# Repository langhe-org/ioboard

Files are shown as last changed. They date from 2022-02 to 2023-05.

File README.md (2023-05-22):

# ioboard

This circuit board is the interface between a Beaglebone Black and the rest of the greenhouse components.

## Ordering

The part numbers in the BOM and CPL included in the release are generated for JLC PCB. Alternative part numbers will have to be used for other fabrication houses.

## Assembly BOM

The following components are not included in the PCBA and must be purchased and soldered on separately:

- 1x CUI PDQE20-Q24-S5-D
- 2x Mornsun BO505S-1RW3
- 8x Phoenix Contact 1945119
- 4x Phoenix Contact 1945122

## Mating Connectors

Part numbers to mate the the headers:

- 8x Phoenix Contact 1984031
- 4x Phoenix Contact 1984345

## Enclosure

This board is designed to be housed in a Polycase WH-16 enclosure.

https://www.polycase.com/wh-16

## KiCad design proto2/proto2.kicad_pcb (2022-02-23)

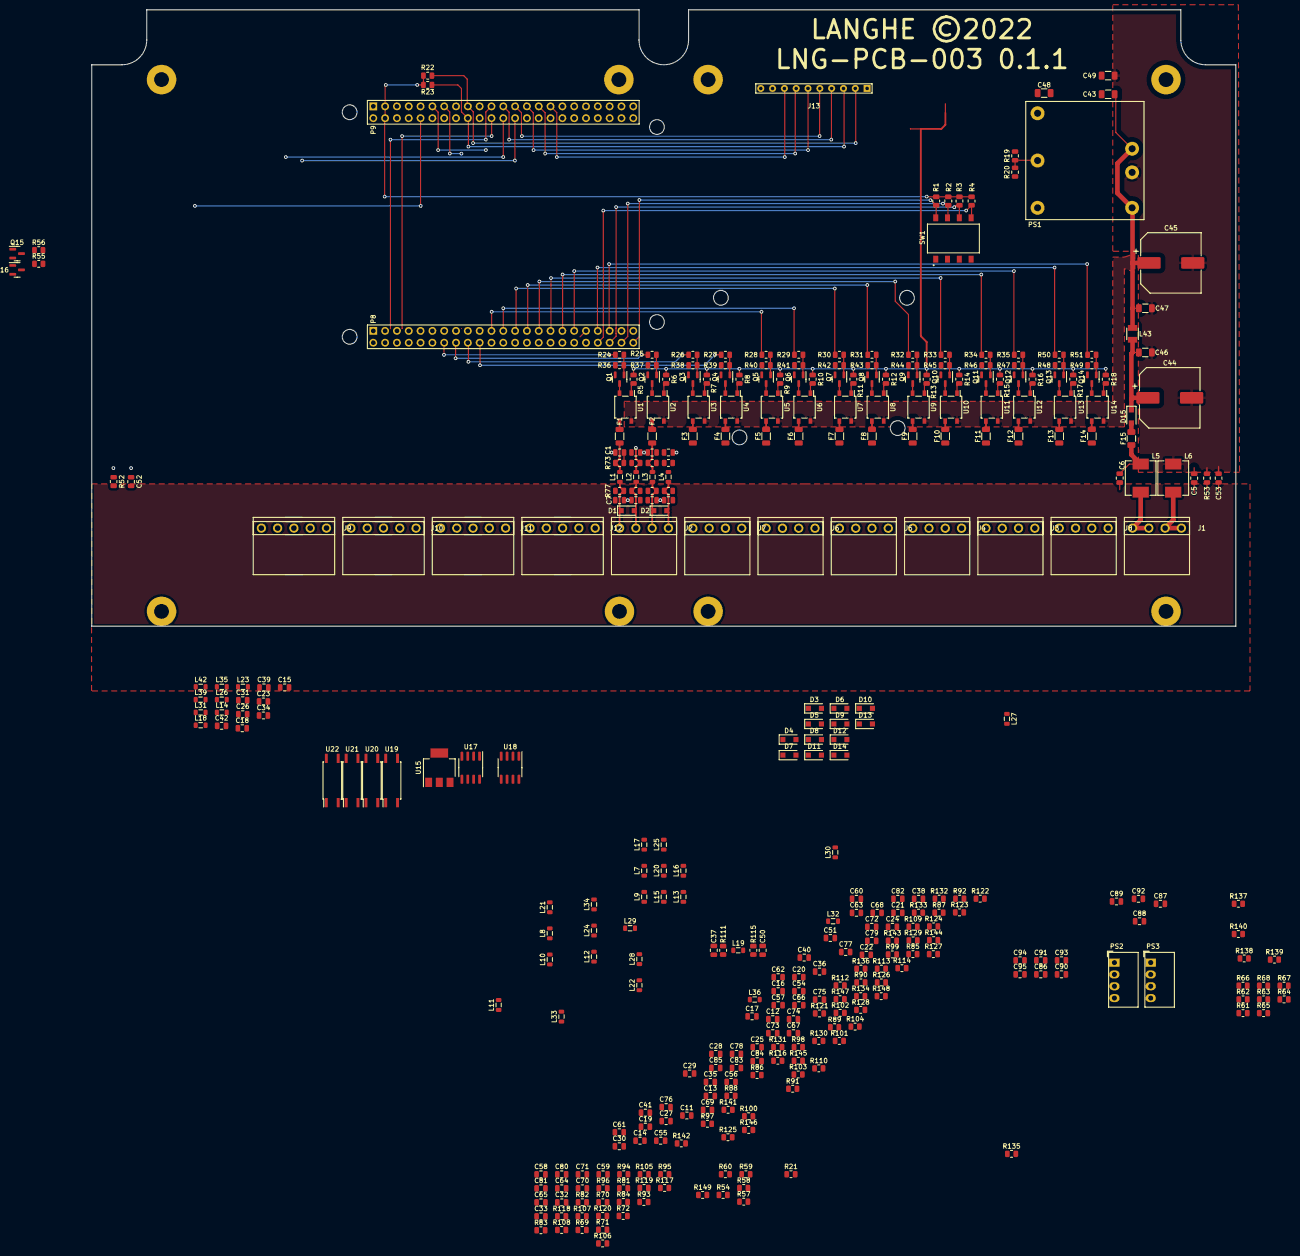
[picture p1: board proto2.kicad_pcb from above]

Board: 4 copper layers, 245.9 x 132.5 mm, 369 parts (0 on the bottom side), 250 nets.

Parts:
BB1: BeagleBone; BeagleBone_UpsideDown
C1, C2, C3, C4, C5, C6, C7, C8, C9, C10, C11, C12, C13, C14, C15, C16, C17, C18, C19, C20, C21, C22, C23, C24, C25, C26, C27, C28, C29, C30, C31, C32, C33, C34, C35, C36, C37, C38, C39, C40, C41, C42, C50, C51, C54, C55, C56, C57, C58, C59, C60, C61, C62, C63, C64, C65, C66, C67, C68, C69, C70, C71, C72, C73, C74, C75, C76, C77, C78, C79, C80, C81, C82, C83, C84, C85, C86, C87, C88, C89, C90, C91, C92, C93, C94, C95: 10uF; C_0805_2012Metric
C43, C49: 1nF 2kV; C_1206_3216Metric
C44, C45: 330uF; CP_Elec_13x12.5
C46, C47: 4.7uF; C_1206_3216Metric
C48: 100uF; C_1206_3216Metric
C52, C53: 0.1uF; C_0805_2012Metric
D1, D2, D3, D4, D5, D6, D7, D8, D9, D10, D11, D12, D13, D14, D15: D_Small_ALT; D_SOD-123F
F1, F2, F3, F4, F5, F6, F7, F8, F9, F10, F11, F12, F13, F14: 0.5A; R_1206_3216Metric
F15: 1A; R_1206_3216Metric
J1: Main Power; Phoenix_Contact_PST_4
J2, J3, J4, J5, J6, J7, J8: Output; Phoenix_Contact_PST_4
J9, J10, J11, J12: Device; Phoenix_Contact_PST_5
J13: Daughter Card; Proto2_DaughterCard
L1, L2, L3, L4, L7, L8, L9, L10, L11, L12, L13, L14, L15, L16, L17, L18, L19, L20, L21, L22, L23, L24, L25, L26, L27, L28, L29, L30, L31, L32, L33, L34, L35, L36, L39, L42: 10uH 500mA; L_0805_2012Metric
L5, L6: 2.2uH 7A; Coilmax_MS0630-2R2M
L43: 2.2uH 1.6A; Murata_LQH32PN2R2NN0L
Outline: Polycase_DC96
PS1: CUI PDQE20-Q24-S5-D; CUI_PDQE20
PS2, PS3: B0505S-1WR3; Converter_DCDC_Murata_MEE1SxxxxSC_THT
Q1, Q2, Q3, Q4, Q5, Q6, Q7, Q8, Q9, Q10, Q11, Q12, Q13, Q14, Q15: 2N7002; SOT-23
Q16: AO3401A; SOT-23
R1, R2, R3, R4, R21, R57, R65, R66, R67, R68: 10K; R_0805_2012Metric
R5, R6, R7, R8, R9, R10, R11, R12, R13, R14, R15, R16, R17, R18: 433R; R_0805_2012Metric
R19, R20: R Trim; C_0805_2012Metric
R22, R23, R137, R138: 4.7K; R_0805_2012Metric
R24, R25, R26, R27, R28, R29, R30, R31, R32, R33, R34, R35, R50, R51, R55, R61, R62, R63, R64: 1K; R_0805_2012Metric
R36, R37, R38, R39, R40, R41, R42, R43, R44, R45, R46, R47, R48, R49, R56: 27K; R_0805_2012Metric
R52, R53, R54, R58, R59, R60, R69, R70, R71, R72, R73, R74, R75, R76, R77, R78, R79, R80, R81, R82, R83, R84, R85, R86, R87, R88, R89, R90, R91, R92, R93, R94, R95, R96, R97, R98, R99, R100, R101, R102, R103, R104, R105, R106, R107, R108, R109, R110, R111, R112, R113, R114, R115, R116, R117, R118, R119, R120, R121, R122, R123, R124, R125, R126, R127, R128, R129, R130, R131, R132, R133, R134, R135, R136, R141, R142, R143, R144, R145, R146, R147, R148, R149: 0R; R_0805_2012Metric
R139, R140: 120R; R_0805_2012Metric
SW1: SW_DIP_x04; CUI_DS04-254-2-04BK-SMT
U1, U2, U3, U4, U5, U6, U7, U8, U9, U10, U11, U12, U13, U14: AQY282SX; SO-4_4.4x4.3mm_P2.54mm
U15: AMS1117-3.3; SOT-223-3_TabPin2
U17: ISO1540; SOIC-8_3.9x4.9mm_P1.27mm
U18: NSI8021N; SOIC-8_3.9x4.9mm_P1.27mm
U19, U20, U21, U22: EL817; SO-4_7.6x3.6mm_P2.54mm

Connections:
3V3_I2C: C91.1, R137.1, R138.1, U15.2 (VO)
5V_I2C: C88.1, C89.1, C90.1, L31.1, PS2.4 (+Vout), R105.1, U15.3 (VI), U17.8 (VCC2)
5V_UART: C94.1, C95.1, L39.1, PS3.4 (+Vout), R117.1, U18.8 (VDD2)
+3V3: BB1.9.3 (VDD_3V3), BB1.9.4 (VDD_3V3), C93.1, R1.1, R2.1, R3.1, R4.1, R21.1, R22.1, R23.1, R65.1, R66.1, R67.1, R68.1, U18.1 (VDD1)
+5V: BB1.9.5 (VDD_5V), BB1.9.6 (VDD_5V), Q16.2 (S), R5.2, R6.2, R7.2, R8.2, R9.2, R10.2, R11.2, R12.2, R13.2, R14.2, R15.2, R16.2, R17.2, R18.2, R57.1, R149.1
+5VP: C86.1, C87.1, C92.1, PS2.2 (+Vin), PS3.2 (+Vin), Q16.3 (D), R149.2, U17.1 (VCC1)
+24V: C43.2, C45.1, C47.1, L43.2, PS1.1 (CTRL), PS1.3 (Vin), U1.4, U2.4, U3.4, U4.4, U5.4, U6.4, U7.4, U8.4, U9.4, U10.4, U11.4, U12.4, U13.4, U14.4
/Inputs/GP_1: R65.2, U19.4
/Inputs/GP_2: R66.2, U20.4
/Inputs/GP_3: R67.2, U21.4
/Inputs/GP_4: R68.2, U22.4
/Power/5V_POUR: R59.1, R60.2
/Power/24V_POUR: R54.1, R58.2
/Power/TRIM: PS1.5 (trim), R19.2, R20.1
BS_1: BB1.8.46 (GPIO2_27), R1.2, SW1.8
BS_2: BB1.8.44 (GPIO2_9), R2.2, SW1.7
BS_3: BB1.8.42 (GPIO2_11), R3.2, SW1.6
BS_4: BB1.8.40 (GPIO2_13), R4.2, SW1.5
BS_5: BB1.9.31 (SPI1_SCLK), J13.8, R21.2
DQ1_1: F1.1, L1.1, R73.1
DQ1_2: F2.1, L3.1, R75.1
DQ2_1: F3.1, L7.1, R85.1
DQ2_2: F4.1, L9.1, R87.1
DQ3_1: F5.1, L11.1, R97.1
DQ3_2: F6.1, L13.1, R99.1
DQ4_1: F7.1, L16.1, R109.1
DQ4_2: F8.1, L19.1, R111.1
DQ5_1: F9.1, L21.1, R121.1
DQ5_2: F10.1, L24.1, R123.1
DQ6_1: F11.1, L27.1, R129.1
DQ6_2: F12.1, L29.1, R131.1
DQ7_1: F13.1, L32.1, R141.1
DQ7_2: F14.1, L34.1, R143.1
GND-PE: C1.2, C2.2, C3.2, C4.2, C5.2, C6.2, C7.2, C8.2, C9.2, C10.2, C11.2, C12.2, C13.2, C14.2, C15.2, C16.2, C17.2, C18.2, C19.2, C20.2, C21.2, C22.2, C23.2, C24.2, C25.2, C26.2, C27.2, C28.2, C29.2, C30.2, C31.2, C32.2, C33.2, C34.2, C35.2, C36.2, C37.2, C38.2, C39.2, C40.2, C41.2, C42.2, C50.2, C51.2, C52.1, C53.2, C54.2, C55.2, C56.2, C57.2, C58.2, C59.2, C60.2, C61.2, C62.2, C63.2, C64.2, C65.2, C66.2, C67.2, C68.2, C69.2, C70.2, C71.2, C72.2, C73.2, C74.2, C75.2, C76.2, C77.2, C78.2, C79.2, C80.2, C81.2, C82.2, C83.2, C84.2, C85.2, J9.5, J10.5, J11.5, J12.5, R52.1, R53.2, R58.1, R60.1
GND-PWR: C44.2, C45.2, C46.2, C47.2, C49.2, C53.1, L2.1, L4.1, L6.1, L8.1, L10.1, L12.1, L15.1, L17.1, L20.1, L22.1, L25.1, L28.1, L30.1, L33.1, L36.1, PS1.2 (GND), R53.1, R54.2, R69.1, R74.1, R76.1, R86.1, R88.1, R98.1, R100.1, R110.1, R112.1, R122.1, R124.1, R130.1, R132.1, R142.1, R144.1, U19.2, U20.2, U21.2, U22.2
GND-SIG: BB1.8.1 (DGND), BB1.8.2 (DGND), BB1.9.1 (DGND), BB1.9.2 (DGND), BB1.9.43 (DGND), BB1.9.44 (DGND), BB1.9.45 (DGND), BB1.9.46 (DGND), C48.2, C49.1, C52.2, C86.2, C87.2, C92.2, C93.2, J13.9, J13.10, PS1.6 (0V), PS2.1 (-Vin), PS3.1 (-Vin), Q1.2 (S), Q2.2 (S), Q3.2 (S), Q4.2 (S), Q5.2 (S), Q6.2 (S), Q7.2 (S), Q8.2 (S), Q9.2 (S), Q10.2 (S), Q11.2 (S), Q12.2 (S), Q13.2 (S), Q14.2 (S), Q15.2 (S), R20.2, R36.2, R37.2, R38.2, R39.2, R40.2, R41.2, R42.2, R43.2, R44.2, R45.2, R46.2, R47.2, R48.2, R49.2, R52.2, R56.2, R59.2, SW1.1, SW1.2, SW1.3, SW1.4, U17.4 (GND1), U18.4 (GND1), U19.3, U20.3, U21.3, U22.3
GND_I2C: C88.2, C89.2, C90.2, C91.2, L35.1, PS2.3 (-Vout), R106.1, U15.1 (GND), U17.5 (GND2)
GND_UART: C94.2, C95.2, L42.1, PS3.3 (-Vout), R118.1, R140.2, U18.5 (GND2)
GP_1: BB1.9.23 (GPIO1_17), J13.4
GP_2: BB1.9.25 (GPIO3_21), J13.5
GP_3: BB1.9.27 (GPIO3_19), J13.6
GP_4: BB1.9.29 (SPI1_D0), J13.7
unnamed: C1.1, R73.2
unnamed: C2.1, R74.2
unnamed: C3.1, R75.2
unnamed: C4.1, R76.2
unnamed: C5.1, R69.2
unnamed: C6.1, R72.2
unnamed: C7.1, R77.2
unnamed: C8.1, R78.2
unnamed: C9.1, R79.2
unnamed: C10.1, R80.2
unnamed: C11.1, R85.2
unnamed: C12.1, R86.2
unnamed: C13.1, R87.2
unnamed: C14.1, R88.2
unnamed: C15.1, R84.2
unnamed: C16.1, R89.2
unnamed: C17.1, R90.2
unnamed: C18.1, R83.2
unnamed: C19.1, R91.2
unnamed: C20.1, R92.2
unnamed: C21.1, R97.2
unnamed: C22.1, R98.2
unnamed: C23.1, R96.2
unnamed: C24.1, R99.2
unnamed: C25.1, R100.2
unnamed: C26.1, R95.2
unnamed: C27.1, R101.2
unnamed: C28.1, R102.2
unnamed: C29.1, R103.2
unnamed: C30.1, R104.2
unnamed: C31.1, R108.2
unnamed: C32.1, R70.2
unnamed: C33.1, R71.2
unnamed: C34.1, R107.2
unnamed: C35.1, R109.2
unnamed: C36.1, R110.2
unnamed: C37.1, R111.2
unnamed: C38.1, R112.2
unnamed: C39.1, R120.2
unnamed: C40.1, R113.2
unnamed: C41.1, R114.2
unnamed: C42.1, R119.2
unnamed: C44.1, C46.1, D15.1 (K), L43.1
unnamed: C50.1, R115.2
unnamed: C51.1, R116.2
unnamed: C54.1, R121.2
unnamed: C55.1, R122.2
unnamed: C56.1, R123.2
unnamed: C57.1, R124.2
unnamed: C58.1, R81.2
unnamed: C59.1, R82.2
unnamed: C60.1, R125.2
unnamed: C61.1, R126.2
unnamed: C62.1, R127.2
unnamed: C63.1, R128.2
unnamed: C64.1, R93.2
unnamed: C65.1, R94.2
unnamed: C66.1, R129.2
unnamed: C67.1, R130.2
unnamed: C68.1, R131.2
unnamed: C69.1, R132.2
unnamed: C70.1, R105.2
unnamed: C71.1, R106.2
unnamed: C72.1, R133.2
unnamed: C73.1, R134.2
unnamed: C74.1, R135.2
unnamed: C75.1, R136.2
unnamed: C76.1, R141.2
unnamed: C77.1, R142.2
unnamed: C78.1, R143.2
unnamed: C79.1, R144.2
unnamed: C80.1, R117.2
unnamed: C81.1, R118.2
unnamed: C82.1, R145.2
unnamed: C83.1, R146.2
unnamed: C84.1, R147.2
unnamed: C85.1, R148.2
unnamed: D1.1 (K), J2.1, L1.2, R77.1
unnamed: D1.2 (A), J2.2, L2.2, R78.1
unnamed: D2.1 (K), J2.3, L3.2, R79.1
unnamed: D2.2 (A), J2.4, L4.2, R80.1
unnamed: D3.1 (K), J3.1, L7.2, R89.1
unnamed: D3.2 (A), J3.2, L8.2, R90.1
unnamed: D4.1 (K), J3.3, L9.2, R91.1
unnamed: D4.2 (A), J3.4, L10.2, R92.1
unnamed: D5.1 (K), J4.1, L11.2, R101.1
unnamed: D5.2 (A), J4.2, L12.2, R102.1
unnamed: D6.1 (K), J4.3, L13.2, R103.1
unnamed: D6.2 (A), J4.4, L15.2, R104.1
unnamed: D7.1 (K), J5.1, L16.2, R113.1
unnamed: D7.2 (A), J5.2, L17.2, R114.1
unnamed: D8.1 (K), J5.3, L19.2, R115.1
unnamed: D8.2 (A), J5.4, L20.2, R116.1
unnamed: D9.1 (K), J6.1, L21.2, R125.1
unnamed: D9.2 (A), J6.2, L22.2, R126.1
unnamed: D10.1 (K), J6.3, L24.2, R127.1
unnamed: D10.2 (A), J6.4, L25.2, R128.1
unnamed: D11.1 (K), J7.1, L27.2, R133.1
unnamed: D11.2 (A), J7.2, L28.2, R134.1
unnamed: D12.1 (K), J7.3, L29.2, R135.1
unnamed: D12.2 (A), J7.4, L30.2, R136.1
unnamed: D13.1 (K), J8.1, L32.2, R145.1
unnamed: D13.2 (A), J8.2, L33.2, R146.1
unnamed: D14.1 (K), J8.3, L34.2, R147.1
unnamed: D14.2 (A), J8.4, L36.2, R148.1
unnamed: D15.2 (A), F15.1
unnamed: F1.2, U1.3
unnamed: F2.2, U2.3
unnamed: F3.2, U3.3
unnamed: F4.2, U4.3
unnamed: F5.2, U5.3
unnamed: F6.2, U6.3
unnamed: F7.2, U7.3
unnamed: F8.2, U8.3
unnamed: F9.2, U9.3
unnamed: F10.2, U10.3
unnamed: F11.2, U11.3
unnamed: F12.2, U12.3
unnamed: F13.2, U13.3
unnamed: F14.2, U14.3
unnamed: J1.1, J1.2, L5.2, R70.1
unnamed: J1.3, J1.4, L6.2, R71.1
unnamed: J9.1, L14.2, R83.1
unnamed: J9.4, L18.2, R84.1
unnamed: J10.1, L23.2, R95.1
unnamed: J10.4, L26.2, R96.1
unnamed: J11.1, L31.2, R107.1
unnamed: J11.4, L35.2, R108.1
unnamed: J12.1, L39.2, R119.1
unnamed: J12.4, L42.2, R120.1
unnamed: L14.1, R81.1
unnamed: L18.1, R82.1
unnamed: L23.1, R93.1
unnamed: L26.1, R94.1
unnamed: Q1.1 (G), R24.1, R36.1
unnamed: Q1.3 (D), U1.2
unnamed: Q2.1 (G), R25.1, R37.1
unnamed: Q2.3 (D), U2.2
unnamed: Q3.1 (G), R26.1, R38.1
unnamed: Q3.3 (D), U3.2
unnamed: Q4.1 (G), R27.1, R39.1
unnamed: Q4.3 (D), U4.2
unnamed: Q5.1 (G), R28.1, R40.1
unnamed: Q5.3 (D), U5.2
unnamed: Q6.1 (G), R29.1, R41.1
unnamed: Q6.3 (D), U6.2
unnamed: Q7.1 (G), R30.1, R42.1
unnamed: Q7.3 (D), U7.2
unnamed: Q8.1 (G), R31.1, R43.1
unnamed: Q8.3 (D), U8.2
unnamed: Q9.1 (G), R32.1, R44.1
unnamed: Q9.3 (D), U9.2
unnamed: Q10.1 (G), R33.1, R45.1
unnamed: Q10.3 (D), U10.2
unnamed: Q11.1 (G), R34.1, R46.1
unnamed: Q11.3 (D), U11.2
unnamed: Q12.1 (G), R35.1, R47.1
unnamed: Q12.3 (D), U12.2
unnamed: Q13.1 (G), R48.1, R50.1
unnamed: Q13.3 (D), U13.2
unnamed: Q14.1 (G), R49.1, R51.1
unnamed: Q14.3 (D), U14.2
unnamed: Q15.1 (G), R55.1, R56.1
unnamed: Q15.3 (D), Q16.1 (G), R57.2
unnamed: R5.1, U1.1
unnamed: R6.1, U2.1
unnamed: R7.1, U3.1
unnamed: R8.1, U4.1
unnamed: R9.1, U5.1
unnamed: R10.1, U6.1
unnamed: R11.1, U7.1
unnamed: R12.1, U8.1
unnamed: R13.1, U9.1
unnamed: R14.1, U10.1
unnamed: R15.1, U11.1
unnamed: R16.1, U12.1
unnamed: R17.1, U13.1
unnamed: R18.1, U14.1
unnamed: R61.2, U19.1
unnamed: R62.2, U20.1
unnamed: R63.2, U21.1
unnamed: R64.2, U22.1
unnamed: R139.1, U18.7 (INA)
OUT_1: BB1.8.14 (GPIO0_26), R24.2
OUT_2: BB1.8.16 (GPIO1_14), R25.2
OUT_3: BB1.8.18 (GPIO2_1), R26.2
OUT_4: BB1.8.20 (GPIO1_31), R27.2
OUT_5: BB1.8.21 (GPIO1_30), R28.2
OUT_6: BB1.8.23 (GPIO1_4), R29.2
OUT_7: BB1.8.25 (GPIO1_0), R30.2
OUT_8: BB1.8.27 (GPIO2_22), R31.2
OUT_9: BB1.8.29 (GPIO2_23), R32.2
OUT_10: BB1.8.31 (GPIO0_10), R33.2
OUT_11: BB1.8.33 (GPIO0_9), R34.2
OUT_12: BB1.8.35 (GPIO0_8), R35.2
OUT_13: BB1.8.39 (GPIO2_12), R50.2
OUT_14: BB1.8.41 (GPIO2_10), R51.2
RESETn: BB1.9.10 (SYS_RESETn), R55.2
RX: J12.3, R139.2
SCL: J11.2, R138.2, U17.6 (SCL2)
SDA: J11.3, R137.2, U17.7 (SDA2)
TX: J12.2, R140.1, U18.6 (OUTB)
VDD: C43.1, C48.1, J13.1, PS1.4 (+Vo), R19.1
VIN: F15.2, L5.1, R72.1
iRX: BB1.9.26 (UART1_RXD), U18.2 (OUTA)
iSCL: BB1.9.19 (I2C2_SCL), J13.2, R22.2, U17.3 (SCL1)
iSDA: BB1.9.20 (I2C2_SDA), J13.3, R23.2, U17.2 (SDA1)
iTX: BB1.9.24 (UART1_TXD), U18.3 (INB)

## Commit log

2021-12-10 Add initial work to repository.
    [conn.sch, inputs.sch, outputs.sch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]
2021-12-15 Routed Board.
    [outputs.sch, power.sch, proto2.kicad_pcb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]
2021-12-16 Added correct cap and moved DIP switches.
    [power.sch, proto2.kicad_pcb]
2021-12-17 Finished routing board and other changes, bad commit message, I know.
    [outputs.sch, power.sch, proto2.kicad_pcb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]
2021-12-18 Reversed the filter order.
    [proto2.kicad_pcb, terminals.sch]
2021-12-19 Updated filters and Power supply foorptint.
    [power.sch, proto2.kicad_pcb, terminals.sch]
2021-12-21 Added note for current draw of SBCs.
    [power.sch]
2021-12-21 Updated drill hole sizes.
    [proto2.kicad_pcb, proto2.sch]
2021-12-23 Fixing the issues the filter-fix merge created.
    [power.sch, proto2.kicad_pcb]
2021-12-23 Removed silkscreen outlines fro BBB and RPi.
    [proto2.kicad_pcb]
2021-12-24 Added schematics following Atlas Scientific's recomended design.
    [EC.sch, PH.sch, Temperature.sch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]
2021-12-24 Added MOSFET drivers for the SSRs, pullups for I2C, and referenced DIP switches to 3V3.
    [outputs.sch, proto2.kicad_pcb, proto2.sch]
2021-12-24 Removed Raspberry Pi, added spacing to terminals.
    [outputs.sch, proto2.kicad_pcb, proto2.sch]
2021-12-28 Replaced LDO with a D2PAK type. Cleaned some traces.
    [power.sch, proto2.kicad_pcb]
2021-12-30 Removed UART board.
    [serial.sch, uart2.kicad_pcb, uart2.sch]
2021-12-30 Added reverse polarity diode.
    [power.sch, proto2.kicad_pcb]
2021-12-30 Created new board design for connected grounds.
    [reservoir2.kicad_pcb, reservoir2.sch, reservoir2_AS.sch]
2021-12-30 New adapter for RPi to BBB boards.
    [rpiadapt2.kicad_pcb, rpiadapt2.sch]
2021-12-30 Updates and changes for production run of 0.1.0
    [power.sch, proto2.kicad_pcb, proto2.sch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]
2022-01-13 Replaced 2N7000 symbol with 2N7002.
    [outputs.sch, proto2.kicad_pcb]
2022-01-14 Replaces board outline with Polycase DC-96 outline.
    [proto2.kicad_pcb]
2022-01-20 Conversion to 6.0 and some minor updates.
    [outputs.kicad_sch, power.kicad_sch, proto2.kicad_sch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]
2022-01-20 Added KiCad 6.0 local project file.
2022-01-21 Added another 2 outputs and re-routed board.
    [outputs.kicad_sch, power.kicad_sch, proto2.kicad_pcb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]
2022-01-28 Added Datasheet links
    [outputs.kicad_sch, power.kicad_sch, proto2.kicad_sch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]
2022-01-29 Removed KiCad 5.1 Files
    [conn.sch, inputs.sch, outputs.sch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]
2022-02-02 Added switch for 5V external devices power based off SYS_RESETn.
    [power.kicad_sch, proto2.kicad_pcb, proto2.kicad_sch]
2022-02-17 Working in suggestions from CFL review.
    [comms.kicad_sch, power.kicad_sch, proto2.kicad_pcb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]
2022-02-17 Reworked board for just one reservoir with isolators and removed temperature.
    [reservoir2.kicad_pcb, reservoir2.kicad_sch, reservoir2_old.kicad_pcb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]
2022-02-17 Changes suggested by CFL.
    [comms.kicad_sch, power.kicad_sch, proto2.kicad_sch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]
2022-02-22 Moved reservoir2 to it's own repo and archived rpiadapt2.
    [EC.sch, PH.sch, Temperature.sch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]
2022-02-23 Laying out new filters and some schematic updates.
    [comms.kicad_sch, inputs.kicad_sch, outputs.kicad_sch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]
2022-02-24 Laying out board. in-process commit.
    [comms.kicad_sch, inputs.kicad_sch, outputs.kicad_sch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]
2022-03-02 Filter layout and some schematic fixes.
    [power.kicad_sch, proto2.kicad_sch, terminals.kicad_sch]
2022-03-07 Final layout for 0.2.0 and various BOM and minor schematic updates.
    [comms.kicad_sch, inputs.kicad_sch, power.kicad_sch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]
2022-03-07 Fixed SSR footprint in schematic and corrected output pinout.
    [comms.kicad_sch, inputs.kicad_sch, outputs.kicad_sch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]
2022-05-30 Rearranged GPIO around the boot pins.
    [comms.kicad_sch, inputs.kicad_sch, outputs.kicad_sch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]
2022-05-30 Moved the board outline so there is more room for connectors. Moved connectors so vertical plugs can be used.
2022-06-07 Added larger fuse for 24V, replaced main polarity diode, and relayed out board to fit new components.
    [comms.kicad_sch, inputs.kicad_sch, outputs.kicad_sch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]
2022-06-08 Added Kicad 6.0 files and *-backups/ folders to the ignore.
2022-06-08 Updated PTC sizes so they will not trip with typical current draw.
    [outputs.kicad_sch, power.kicad_sch, proto2.kicad_sch]
2022-07-26 Changed revision on schematic to 0.3.0.
    [comms.kicad_sch, inputs.kicad_sch, outputs.kicad_sch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]
2022-07-26 Changed board outline to Ploycase WH-16 and revision to 0.3.0.
2022-08-04 Updated part number for F15 and D15.
    [power.kicad_sch]
2022-08-04 Updated F15,D15,U1-14 to parts in stock at JLC. Updated U1-14 footprints to more common size.
    [comms.kicad_sch, inputs.kicad_sch, outputs.kicad_sch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]
2022-09-19 Rerouting outputs, adding integrated analog input.
    [comms.kicad_sch, inputs.kicad_sch, outputs.kicad_sch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]
2023-05-20 Removed some old backups and files from older Kicad versions
2023-05-20 Converted files to Kicad v7.0.2
    [comms.kicad_sch, inputs.kicad_sch, outputs.kicad_sch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]
2023-05-20 Changed paper size and some text on the titleblocks
    [comms.kicad_sch, inputs.kicad_sch, outputs.kicad_sch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]
2023-05-20 Removed part number from board
2023-05-20 Changed internal references from proto2 to ioboard
    [comms.kicad_sch, inputs.kicad_sch, outputs.kicad_sch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]
2023-05-20 Ranamed files from proto2 to ioboard
    [ioboard.kicad_sch]
2023-05-20 Renamed directory from proto2 to ioboard
    [comms.kicad_sch, inputs.kicad_sch, ioboard.kicad_sch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]

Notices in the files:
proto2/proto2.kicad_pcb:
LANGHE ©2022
